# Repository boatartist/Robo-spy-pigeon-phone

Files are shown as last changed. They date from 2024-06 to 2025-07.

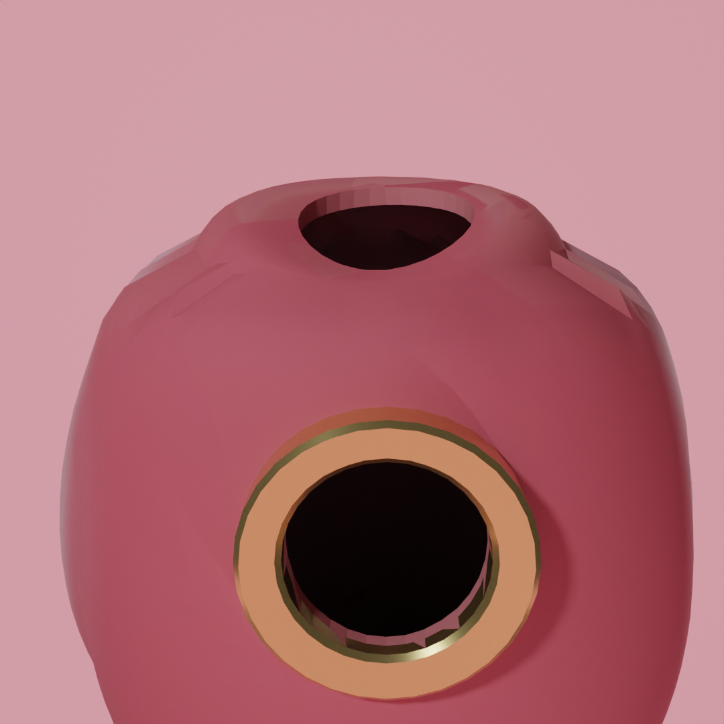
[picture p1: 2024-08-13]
Darcy_renderings/birbodyholetop1.png

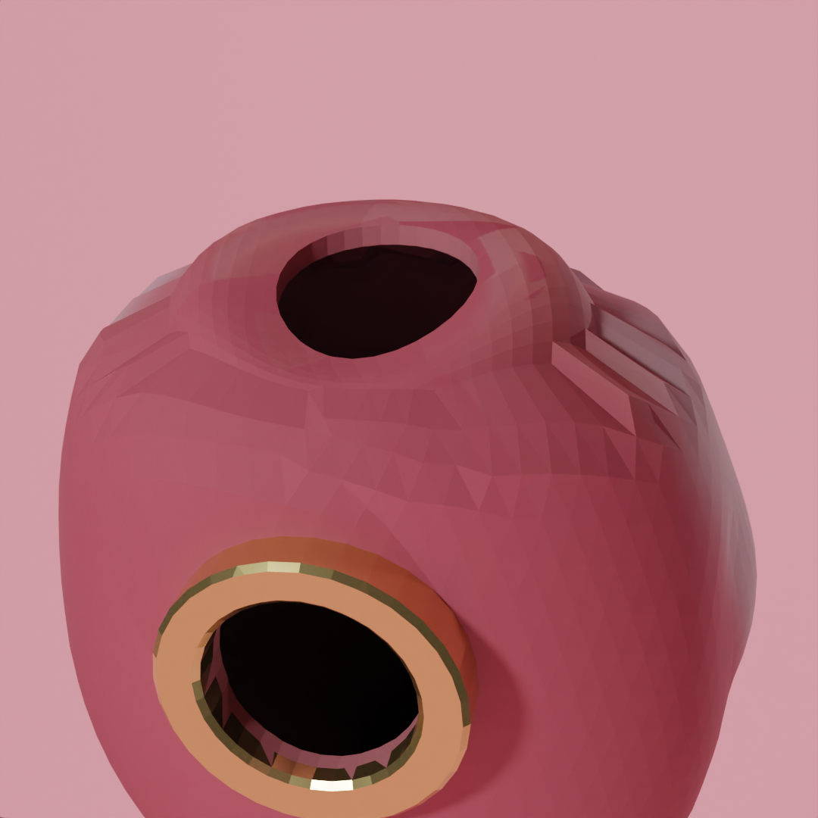
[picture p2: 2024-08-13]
Darcy_renderings/birbodyholetopflat1.png

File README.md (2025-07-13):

# Robo-spy-pigeon-phone
## May 16, 2024
Hello, welcome to my Robot-spy-pigeon-phone-assistant-project! (I'm bad at names I'll fix it later)
This is an idea I've had in my head for ages, and I really want to document one of my procrastination projects properly, so I'm just going to put everything I do onto this github, then procrastinate on my procrastination by fixing it later. 

So, robot phones. I think I was unreasonably influenced by Amy McCulloch's Jinxed series, which is a pretty good YA series in its own right. Basically the premise is that everyone has an animal-looking robot that does everything their phone used to do, and also is like a pet and friend and assistant, and idk I just think that's pretty cool. I would just make that but it'd kinda feel like plagiarism or something, which brings me to my second influence: Birds aren't real. I assume everyone has heard of this pseudo conspiracy, which is just hilarious and very much something my generation would make up in response to actual conspiracy theorists. Essentially, all birds were hunted down and killed by the US government/CIA in the 50s and 60s and replaced with spy drones that are tracking us, ooh scary. Finally: ornithopters. You know drones? They're like that but cooler, because they flap their wings. I'm not an aeronautical engineer (I'm just a highschooler actually), but I do have a very hyper plane loving little brother, so there's that

With these ideas in mind I have a bunch of features I want to implement at some point but may never, best explained through a series of tiny sketches:

WIN_20240516_12_24_25_Scan
WIN_20240516_12_25_56_Scan

Look at the little cyborg pigeon!!!❤️❤️❤️❤️ I'm so proud of my non-existent drawing skills. If you can't read my handwriting (valid, I can't either), here's some of the highlights:

- cute little perch
- holds a little pencil
- camera (or is it a death laser?)
- touchscreen
- eyes follow you around
- full 360° vision, head rotates
- foot clamps/jointed toes (taking inspiration from nerdforge's prosthetic finger but it defaults to contracted so it doesn't fall off the perch)
- Bits that move (perched edition): feet lift and flap, head rotates = 3 servos, optional bonus: balance body by tilting
- also some sound effects/comments ie. eeeee, creeeeak, ring ring..., unknown phone number...

## May 28, 2024
I made a super cute lil cardboard/electrical tape model, feeling very professional
WIN_20240528_18_45_05_Pro
And if the ultra-high quality school laptop night photo didn't sell it to you, then I used an AAA battery as a stylus to sketch over it 🙃


I also found some old(er) sketches and plans from when I wanted to make a cockatoo, so might as well put those in, there's no one reading this anyway lol

<!-- ![WIN_20240528_20_20_27_Scan](https://github.com/boatartist/Robo-spy-pigeon-phone/assets/78235705/01198416-49a5-4d13-a8f2-95e78d5ec8a3)
I probably shouldn't include that last one actually, it's kinda ruining the sci-fi super villain aesthetic I keep imagining. I don't wanna be strutting around with my cool pirate parrot pigeon phone on my shoulder acting all fancy and then get jump-scared by my 16y/o late night ramblings, but whatever. -->

## June 02, 2024 (I think, this is a retrospective post)
I tried to make a bird shape in solidworks and it went disastrously wrong. Luckily my dad is a literal designer so he showed me how to do it and mine are still terrible but i got some ideas about how to do it, later. This was the dumpy model my dad whipped up in like 10 minutes, I think mine are right at the bottom of the windows rubbish bin.



## June 09, 2024
~~Feet! (No not like that stop being dirty minded).~~ (This joke has been redacted because everyone keeps judging me (valid ig)). I figured this was as good a place as any to start my project, so I've spent this weekend wasting filament and masking tape on prototypes, until I got to a design that I think will do for now. My original concept was inspired by prosthetic finger designs (Shout out to [this video from Nerdforge](https://www.youtube.com/watch?v=ZVqa7j6jG0Q) for the inspiration), which contract when a string is yanked and then have a bit of elastic which defaults them to open again. Obviously a bird clinging to a perch for dear life has quite the opposite motivations, so my design had a bit of string on the outside which gets pulled by a servo to open the claws and then a piece of elastic pulling them closed again, as can be seen in this low-res night photo.
WIN_20240609_19_17_24_Pro
This design seemed great on paper but left more than a little to be desired in real life, so I created a new design featuring the coolest thing I know nothing about: gears. After a loooong time in solidworks I finally got something that kind of works, so my current foot design looks like this:
WIN_20240609_19_19_10_Pro
WIN_20240609_19_18_48_Pro
I'll put the current cad files up if there's anyone interested (that's a little inside joke because there's noone here at all lol)

## June 16, 2024
I figured out how to get blender on my school laptop and I've finally got a terrible low-poly model which I'm going to polish up in Solidworks (stl file up now)



This is a photo of a tiny 3D print I did of it, just for fun, I think it looks pretty good.
WIN_20240616_14_55_46_Pro
I also realised that I haven't put up the fancy drawings I did, oops, here they are now.
WIN_20240616_11_46_52_Pro
Umm, what else? Oh yes, I bought a [usb modem](https://www.telstra.com.au/internet/mobile-broadband/prepaid/4gx-mf833v-usb) to use instead of the raspberry pi hat I had for my phone project, which unfortunately broke. Hoping that having an actual professional thing will make this a bit less dodgy. 
I'm also going to buy [a little round touchscreen](https://core-electronics.com.au/128inch-round-lcd-display-module-with-touch-240240-pixels.html), which I'm really excited about, hopefully we start getting some actual progress soon!

## June 18, 2024
Welcome to the total of 2 people I shared the link to this with, here's the things I did today and at the end of the weekend.
1. I chopped the blender model in half and hollowed out the head so I could put a raspberry pi camera in there, the stl can be found on this github but it's not a final product by any means.



2. I bought a cheap usb cable and a usb socket which I soldered together so that the modem doesn't have to stick straight out of the side of the raspberry pi, instead I can attach it via the dodgy cable and position it around the side. I would advise anyone thinking of copying this project to invest in an official cable ([like this one maybe](https://www.amazon.com.au/Degree-Angled-Female-Extension-Adapter/dp/B015H0KUEI?th=1)), I melted quite a lot of plastic and had to restart several times from fragile cables breaking.
WIN_20240618_19_49_22_Pro
WIN_20240618_19_50_09_Pro

## June 25, 2024
I'm away from the Raspberry Pi rn so I can't test this code, but I've been researching text-to-speech (tts) modules that I can use, because a big feature of the bird is that it's going to give audio notifications and users will be able to converse with the robot instead of just using the screen.
WIN_20240709_15_02_11_Scan
After much consideration, I've decided to use the Google tts API (gTTS), following [this Geeks for Geeks article](https://www.geeksforgeeks.org/convert-text-speech-python/) because I'm lazy and it looks easy, but also it's really well documented and I can also use the google speech-to-text API so it will look symmetrical in my brain. According to the tutorial, this is the python code I'm going to need:
```
from gtts import gTTS
import os
tts = gTTS(text='Hello World', lang='en', slow=False)
tts.save('audio_file.mp3')
os.system('start audio_file.mp3')
```

## June 27, 2024
I got the gTTS module working, and I'm using the pygame mixer to play audio through the audio jack. I found an old pair of headphones and a speaker from a singing birthday card which I brutally massacred to make this speaker setup I can plug into the audio jack. I might replace the speaker because it's still a little too quiet, but it works for now. 



In the past I've tried to find a ready-made speaker which would do this for me, but most speakers seem to be the massive round bluetooth speakers, so anyone copying this project I would advise to find a cheap headphone jack part and a small speaker component, that seems like the best option. 
I also improved the head cad file so that the camera fits better and there's also a hole in the other eye for a 5mm led, which I think is pretty cool. I'll upload the new stl alongside the old one, they're pretty similar at this stage. I think the next step is going to be getting my hands on that round display, and also looking at how I'm going to get the microphone working, stay tuned!

## June 30, 2024
Oops, turns out I did not the gTTS working, it steals its tts from the interwebs, and mine is a bit sketchy rn, so I'm settling for a worse module that's fully offline, [pyttsx3](https://pyttsx3.readthedocs.io/en/latest/engine.html) (I did try to install it's updated sibling pyttsx4 but I'm not bothered to install the module on a computer with internet and then manually install it on the raspberry pi, so we're settling for the one I managed to get). The voices are terrible, but at least it talks and I haven't had any major issues. I also don't need to use the pygame mixer to play my sounds, so that's nice. This is my current code: 
```import pyttsx3
engine = pyttsx3.init()
# reducing the speed of the voice from 200 to 100
engine.setProperty('rate', 100)
# I think the english voice is the best, but there's code in the documentation to loop through every voice and test it if you want to find a better one
engine.setProperty('voice', 'english')
#say the thing
engine.say('Hello World, I am pigeon')
#I think the say() method preloads the audio to the engine, and then this method actually runs it 
engine.runAndWait()
```
Oh and here's a photo of the new head, it's still goofy, but I kinda love it.


## July 2, 2024
A quick moment of silent for my realisation that the raspberry pi audio jack does not support the microphone, so I apparently wasted my money and time buying [a new 4-poled plug](https://www.jaycar.com.au/3-5mm-gold-plug-4-pole/p/PP0138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), soldering 4 wires to it and trying to connect the speaker and the microphone to it, ouch. At least I did realise how I could amplify the volume of the speaker using a transistor so now we have this snazzy and compact little set-up on the back of the speaker:



And since I'm overcompensating for my laziness and refusal to make wiring diagrams for my actual school software projects, here's one I whipped up in two minutes:



So it's a bit sad that I did all that for nothing, but at least I have a good result. For now, I'm using a big flat usb mic I bought for a past project that didn't work out, but it's better than nothing until I figure out how to make my own, more compact version with the tiny microphone I bought. Oh and if anyone ever copies this project, [you can get audio output from the gpio pins](https://wiki.batocera.org/audio_via_gpio_rpi_only), which I've been searching for for ages and only discovered after hacking together my solution :( Anyway we live and we learn ig. 

## July 3, 2024
❤️ [http://apachepersonal.miun.se/~muhimr/index_files/Tutorial_4g_modem_with_Raspberry_PI_B_plus.pdf](http://apachepersonal.miun.se/~muhimr/index_files/Tutorial_4g_modem_with_Raspberry_PI_B_plus.pdf)

## July 4, 2024
I was pretty rushed when I posted that article yesterday, I hadn't done much and I just wanted to share the brilliant pdf which unlocked my ability to actually use the usb modem I've bought. So basically what I learnt is that when you go to [192.168.0.1](192.168.0.1) on any device, it takes you to your modem's page, where you can see different diagnostics, change settings and even (if you have a sim-based modem like mine) send and receive text messages. Amazing! This is the best news I've had in ever, because I thought I was going to have to hack together a solution, bypass a billion safeguards and do all sorts of wizardry to even get internet working with the modem, let alone sms on it, but no, I just need to figure out how to steal data from that webpage, praise the lord, god is good, I'm converted, all that jazz⛪✝️

... Actually, maybe not, looks like the website is kind of janky and it doesn't want me to steal from it, or maybe I'm just bad at requests and Beautiful Soup, we'll see. Oh side note I finally ordered the touchscreen watch display yesterday, so it should be here in a few days, and once it arrives I'll have all the components to start building the body (I think), stay tuned!

EDIT: I must apologise to everyone I have mislead in my claims that I was using a singing card's speaker, that **was** the speaker I experimented with, the one I'm currently using comes from a build-a-bear. I found the official product names for both (the singing card speaker is more or less [COM-15350](https://www.melopero.com/en/shop/sensors/audio/thinspeaker0dot5w/) and the build-a-bear speaker is probably [13ry328qf203](https://www.amazon.com.au/Aexit-Electroacoustic-External-13ry328qf203-Loudspeaker/dp/B07BDPJTB2)), as they seem like good options until I find a real product, but I will be using the measurements for the build-a-bear speaker in my CAD modeling.

## July 7, 2024
I was fooling around with my tts function and the audio randomly stopped working, which prompted me to have a small mental breakdown and also transfer my speaker to the GPIO pins, adding 
```dtoverlay=pwm,pin=13,func=4``` to the bottom of `/boot/config.txt`. In the end the actual problem was that raspi-config sometimes likes to have little menty-B's and change pretty standard settings, so I had to go into the system settings and [change the output back to jack](https://www.raspberrypi.com/documentation/computers/configuration.html#audio-2:~:text=passphrase%22%200%200-,Audio,-Specify%20the%20audio). Well that's good to know I guess, and it looks pretty cool and saves needing external batteries, so I'm (kinda) glad it happened. 

![image](https://github.com/boatartist/Robo-spy-pigeon-phone/assets/78235705/21720103-b9aa-44c0-8042-e7db532cf4d5)

In other news I spent way too long being bad at try-except statements and kept getting confused when raising an error caused an error to show up, but in the end I made a quick function to check for internet connection, which will be useful to switch between voices (gTTS is sooooo much better than pyttsx3, but it needs interwebs), or just to prevent errors when looking for texts or other web-based things. 
```import requests
try:
  req = requests.get('https://github.com/boatartist') #shameless self-promo
except:
  print('Uh oh no interwebs')
  #do something else here
```
Lastly, I was annotating and collating notes from the demo python code for my round display which is coming tmw (probably), I might put up those notes in future.

## July 8, 2024
EEEEEEEEEEEEEEE!!!! I just got the display and it's so cute! I'm obsessed. It is very good and once you figure out the code it's pretty intuitive, I'm going to put up a guide at some point, mostly to remind myself, but for now here's how it (more or less) works, based on [the python example](https://files.waveshare.com/upload/b/bb/1.28inch_Touch_LCD_Demo.zip) from [the official wiki](https://www.waveshare.com/wiki/1.28inch_Touch_LCD#Raspberry_Pi_User_Manual) (thank you Waveshare ily <3):

(nvm I moved it to a file of its own because I kept coming up with improvements, check out the code example in `code/round_display_demo.py`)

## July 9, 2024
I *think* that I've finally gotten to the bottom of the stupid audio error, which was based on the raspberry pi not defaulting to the right output, after completely overhauling my entire tts setup haha. In trying to fix my setup, I've moved to a different tts module (again), which is espeak. Actually I didn't really change anything, I'm just using the command line interface rather than the pretty library setup to run it for me. What I did was identify the sound card and device number of my speaker by running `aplay -l` in the command line, and then to output text I give the command line this: `espeak "Some text" -s 120 -ven+f3 --stdout | aplay -D hw:2,0`, which is a lot of fancy symbols for, "espeak please say 'some text' at 120 wpm with the third english female voice" followed by "aplay please play this out of sound card 2 device 0". Oh yeah I found more voices which is nice, I can even make it ✨whisper✨ ooooooh. So that's fun. 

In other news my round display is working great, I made a class for it so I didn't have separate touch, display, image and draw objects, I'll post that in the code folder. At the moment I'm working on making a menu that shouts at you but doesn't keep shouting (I don't know why it won't shut up 🫠), but at least we're going somewhere. I also found that there are lots of pretty colours, because PIL uses the html colour list, which is very expansive and a great opportunity for me to demonstrate my lack of graphic design skills, yay!
Here are some photos from my experimentation:





## July 11, 2024
Yesterday my brain said: "Do some CAD modeling", so I did that even though I didn't have a mouse or any plans, leading to the jankiest prototype ever, but I've got a mouse-adaptor now so I'm going to fix it, but for now I'll put up all the files in a folder:





## July 22, 2024
It might be easy to think, from the fact that I haven't updated this page in 11 days, that I've been busy doing schoolwork and not procrastinating, but no that would be a mis-guided naive optimism. In fact, I told myself that I would not work on this project until I'd finished my homework, which was a sure-fire way to ensure I worked on it constantly during momentary lapses in my willpower. So, what have I achieved? 
1. I made a blocky little case to think about positioning and hold the screen up while I messed around with some code, not sure if it was worth it but it looks cute (or it did before I melted holes in it for all the ports I forgot I needed access to).
   


2. The audio stopped working (again) and I realised that, although using the GPIO pins is very convenient, it only produces square wave digital outputs, which is a bit too janky, so I reverted to using the 3.5mm jack, which is a bit annoying but it does link to my next point
3. I thought a **lot** about how the user could change between audio output modes, experimenting (unsuccessfully) with having a bluetooth mode, which I might come back to later, but in the end I came up with a decent solution, which basically has a socket into which you can plug in wired headphones at any time, they don't turn off, and also a switch/settings option to turn off the built-in speaker by way of a GPIO pin which provides power through my fun transistor solution from earlier.
4. So obviously that meant that I bought a 3.5 mm socket, a usb socket, a couple of switches, and a prototyping solderable board. That last part is the most useful, as it lets me combine all the components, and it was also incredibly convenient because I put all the pins from the display in a line, so I no longer have to worry about the fiddly order every time.


I think I messed up the speaker somehow, might be the transistor, but it's looking better already.
WIN_20240722_13_20_55_Pro
WIN_20240722_13_20_48_Pro

Once I've fixed the built-in speaker I'm going to install the sockets and switches, which will be able to be moved to wherever I want my peripherals, I'm thinking under the wing in the final product, that would be cute. Another plan I have for the end is to get a custom PCB made, which will plug all my components in really nicely and easily, and look a bit smaller and more professional, but I should probably get my prototype working first. I feel like there was some code I did, but I don't think I have any big updates.

Oh, that's right, I wanted to shout out the guys at Core Electronics, the online store where I've been buying a lot of my stuff, because I sent them a really wacky and unedited email asking them whether this project might be worth getting published on their projects section one day, and they came back in a couple of days with a really helpful and encouraging email about how I could transform this blog/log thingo into a proper tutorial, which I'm really grateful for and will definitely be applying when I get around to finalising all the documentation. Thank you! :) 

## August 4/5, 2024
The speaker not working was apparently just because I used the wrong transistor by accident, oops. I think it would have worked if I'd turned it around, but for consistency's sake we're sticking with the BC557, which is a PNP rather than the NPN BC547 I accidentally used. So that's good news, we now have the speaker shouting at us, and it turns off when it's not, so that there's no buzzing.
WIN_20240804_15_00_18_Pro
This means that I almost have enough functionality to mock up another prototype, but I might quickly solder my sockets first, and put in some header pins for servos. I am a little worried because I only have about 3 GPIO pins, since the prototyping board only includes the first half of the pins, but I think this should be enough to do claw movement and maybe head rotation, which is quite exciting. 

Things I need to fix/do (as of my brain rn):
- solder all sockets (3.5mm audio and usb input, maybe hdmi at a later date)
- stop the screen from freaking out and thinking that I'm infinitely pressing wherever I last pressed, I just want to press once and then it stops
- get a useable requests interaction with the modem's webpage, so that I can send and receive texts without using minicom, since the fancy modem is based on windows software. (alternatively I could invest in a less sophisticated/linux compatible modem that does use minicom)
- look at making a pcb/getting a new and bigger prototyping board
- figure out camera -> display live streaming, this should be possible but it doesn't seem to like it
- consider balance, weight and how complex the design should be, so that I stop wasting filament and am more consistent with my design
- possibly remarket the pigeon as a galah, because they're much prettier, their heads are bigger and closer to their bodies, and if I sell them in Australia one day I can frame it as a limited edition native birds line
- start documenting this project properly before it gets too chaotic (I probably won't do this tbh)

## August 11, 2024
I figured out how to stop the display taking infinite input, by reasoning that it probably wasn't a problem unique to my project, and that it likely just doesn't reset to 0,0 ever, despite my best hopes. Basically, when you press the display once, it reads that and keeps outputting it forever, or until there's a new input. To counter that I kept track of the previous input and have a flag which says if there's been any new input to worry about.

With this problem under control, I optimised (slightly) my code and put it in a class, I'll replace previous code uploads with the working current files, you can turn the speaker on or off, change the wifi mode, and listen to the speaker scream at you if you press any function which isn't active yet, I'm pretty impressed with myself. `bird.py` is the main file, and it imports all the other modules including `offline_tts`, `display`, `wifi` and `check_for_internet`. Remember that display also imports the display's module, so if anyone is running this and getting errors, it's probably that. At some later date I'll look into how requirements.txt files work, because there are a lot of random modules to import, and if anyone is ever copying this project I don't want them to have to debug everything line by line. 

I also implemented the camera app, apparently the only thing I needed to change was refreshing the stream every time, but it now works, showing an only slightly laggy feed from the camera, which saves to `final.jpg` on the Desktop (or wherever the main file is) when you click the screen, I'm pretty happy with it. :)

I still don't have a plan for the modem, I think I might have to put my issue on stack overflow, but that's definitely a last resort. In the meantime, I'll keep weighing up the value of just getting a software-less modem, stay tuned!

## August 13, 2024
I am incredibly excited rn, because I showed this project to my awesome friend Darcy a little while back, and she's offered, with all her amazing DT, CAD and Blender skills, to design all the cases for my newly rebranded galah, because she actually knows how to make it look incredible. I'm going to have to give her all the specs, but she's already mocked up a ✨stunning✨ aesthetic prototype, look at it!!! I'll put all the screenshots/renders she sent me in a folder, but here are some of the highlights :)
Birb1angle
Birb1front
birbflat1
birbodyholetopflat1
birhed1

EDIT:

Stack Overflow is the best thing ever and I may have solved all of my modem problems. Literally, I posted [a question](https://stackoverflow.com/questions/78864009/is-there-a-way-to-access-the-sms-capabilities-and-modem-webpage-of-a-usb-4g-mode) and mere minutes later a response from a bored computer scientist popped up, suggesting that I use Selenium to dynamically load the webpage, which I think might be exactly what I needed, so good!

## August 14, 2024
Heh heh heh, it's 9pm on a school night and I only just managed to install all the correct drivers for selenium, but (I think) it's finally ready to actually use, yay! I spent just a little itsy bit of time crying dejectedly when the raspberry pi was being a stupid little child and not being okay with any of the normal procedures, but after searching up something along the lines of 'How to Selenium Raspberry Pi Python beginners easy guide diy step by step someone else do it for me' I *finally* found [a useful tutorial](https://patrikmojzis.medium.com/how-to-run-selenium-using-python-on-raspberry-pi-d3fe058f011). No well actually it was [the link in the comment on that tutorial](https://ivanderevianko.com/2020/01/selenium-chromedriver-for-raspberrypi) which solved my problem but whatever. If anyone wants to know how to install selenium and all it's required drivers, here's what I've learnt (against my will), as a quick 2-step method.

Step 1: Install the actual Selenium module: `pip3 install Selenium`

Step 1.1: Doubt yourself when this doesn't immediately work and install all sorts of different versions, only to realise that this was not at all the problem

Step 2: Try to install all manner of legitimate Firefox and Chrome drivers

Step 2.1: Get desperate and try illegitimate and vaguely sketchy installation methods for said drivers, looking for the right version which matches the version of your browser (you can find what this should be with `chromium-browser --version`)

Step 2.2: Find a more genuine way and finally get the right driver which magically has the correct version and you didn't need to scroll through 50 pages of releases `sudo apt-get install chromium-chromedriver`

Step 3 (extra fun bonus): Use `chromedriver --version` to check that you've got it right all in one and try to push back exhausted tears as you rush to document this because otherwise it's bound to get lost and have to be re-done. Yippee! 🙃✨❤️ 

While I was being optimistic and hadn't tested for base functionality I started coding a function to log into and retrieve data from the website, so I might be able to finish it tmw and implement it slightly, but it's 9.25, I should probs go to bed now.

## August 15, 2024
So, even though Selenium and I are besties now, the telstra webdesign people are my opps, with their user-friendly complex html layouts, unbelievable, smh. I would like to introduce these people to high school students and the level of complexity that there is not in any of my html endeavours, but I guess I'll just have to deal with it. It is going relatively well tho, and for paranoia about losing files sake I'm gonna paste the dodgy thing I've got here: 
```
#password input: id=txtPwd, password = Admin
#login button: id=btnLogin
#each text conversation on the main page's id starts with smslist-item- then a long number
from selenium import webdriver
from selenium.webdriver.common.keys import Keys
from selenium.webdriver.common.by import By
import time

print('installed the things')
#driver = webdriver.Chrome(ChromeDriverManager().install())
#driver = webdriver.Chrome('/usr/bin/chromedriver')
driver = webdriver.Chrome()
print('driver exists')
driver.get('http://192.168.0.1/index.html')
print('got a webpage')
try:
    login = driver.find_element(By.ID, 'txtPwd')
    login.clear()
    login.send_keys('Admin')
    login_button = driver.find_element(By.ID, 'btnLogin')
    login_button.click()
except:
    pass
while True:
    try:
        sms_link = driver.find_element(By.LINK_TEXT, 'SMS')
        sms_link.click()
        break
    except:
        pass
try:
    right_sms_mode = driver.find_element(By.LINK_TEXT, 'Device SMS')
    right_sms_mode.click()
except:
    pass
while True:
    try:
        new_sms_button = driver.find_element(By.ID, 'smslist-new-sms')
        new_sms_button.click()
        break
    except:
        pass
while True:
    try:
        contact_input = driver.find_element(By.ID, 'chosenUserSelect_chzn')
        contact_input.click()
        break
    except:
        pass
contact_select = driver.find_element(By.CLASS_NAME, 'chzn-results')
contacts = {}
try:
    for i in range(59):
        person = driver.find_element(By.ID, f'chosenUserSelect_chzn_o_{i}')
        name = person.get_attribute('value')
        contacts[name] = f'chosenUserSelect_chzn_o_{i}'
except:
    pass
for name in contacts:
    print(name)
contact = input('Contact: ')
contact_input = driver.find_element(By.ID, 'chosen-search-field-input')
contact_input.send_keys(contact + Keys.RETURN)
message = input('Message: ')
text_input = driver.find_element(By.ID, 'chat-input')
text_input.send_keys(message)
send_message = driver.find_element(By.ID, 'btn-send')
send_message.click()
time.sleep(60)
driver.close()
```

So ja, it's a bit special and sometimes it lags a whole bunch so I have to implement dodgy loops, but this code *mostly* works, except for some reason the contacts don't like me and that's still broken, but I can navigate to the texts page and try to send a message, just to nobody. So yay! 

Oh and I also remembered, I'm gonna take my setup to school tmw and Darcy might have a look at measuring and designing stuff (maybe). 

## August 23, 2024
I bought [a super cheap usb microphone from officeworks](https://www.officeworks.com.au/shop/officeworks/p/otto-usb-c-wired-lapel-microphone-otcck15lm) to look at getting speech-to-text, and I can now record audio and interpret it using the speech-recognition module and google speech recognition. However, I didn't have much luck with the module's built-in microphone, and I don't want to have to rely on an internet connection to be able to talk to the robot. So then I messed around with mozilla deepspeech and sopare, and neither of those were very good either. I was just about to give up when I found [vosk](https://alphacephei.com/vosk/), which is a miracle and now I have speech to text:
```
import os
import time
def get_audio(length=5):
  os.system('arecord --device=hw:2,0 --format S16_LE --rate 48000 --duration={length} test.wav')
  print('got audio')

def translate():
  try:
    os.system('vosk-transcriber -i test.wav -o test.txt')
    f = open('test.txt', 'r').read().strip('/n')
    return f
  except:
    print('error')
    return None

while True:
  input()
  get_audio()
  time.sleep(2)
  translate()
```
This isn't implemented yet because I'm not really sure what the best way to record the audio is, whether I can tie it to a button being held down or record for a set time after recording, or whether it's best to listen all the time. Not hugely keen on the last two, but we'll have to see what I dig up. My solution is also quite file-heavy, but I think it should be possible to bypass the audio file like with the tts, we'll see.

## August 24, 2024
I finally got around to changing the settings page to include an internet status and abandoned the idea that you might plug in headphones to a literal bird. I also made a very janky little interface for the notes app where you can speak for 5 seconds and get some text saved to a file, just as a proof of concept really, it's not very useful rn. But I'm feeling very happy that I unlocked another feature, even if it isn't perfect. The stt functions and updated code have been uploaded, and I also uploaded a requirements.txt file. I found a geeks for geeks article which had an automated function to create one, so this is just what it spat out from the folder of all of my code, but this doesn't include command line modules that I access through the os module, and assumes that you run all the code as it exists in the code folder on this github, including having the display functions in the lib folder, so I'll see how I can improve it to make it more useful later on. Anyway, here's some photos of the most recent interfaces (I think I wasn't close enough to the mic, it doesn't seem to have picked up my 'hello this is some test audio' very well but at least it got something) :





## September 04, 2024
I've spent a *lot* of time recently researching power methods, because it occured to me that this is going to need to be wireless, and the shape of the thomas the tank engine battery pack we found in the park isn't going to cut it. 



So I need to make my own battery charger circuit. There are heaps of boards online, and my only requirements are that they supply at least 5V and 2.5A, and have sockets for charging and powering the pi. [This one from Core Electronics](https://core-electronics.com.au/mp2636-power-booster-charger-module.html) looks pretty good, but I'm not 100% sure if that's the best option. If I get that board or similar, I can use a few rechargeable Li-ion batteries from my local Jaycar, but I can also get some online if there's a different shape I need. 

Another option, which seems just an itsy bit dodgy is to use this board I stole from an old drone:



It's super tiny, which is great, but I have no idea if it will work or just catch on fire. At any rate I'd have to botch together a supicious cable for powering the Pi. Also, I just read the specs from the battery casing (I had to bin the original battery because it was on the brink of explosion), and it says that it outputted 3.7V and 600mAh. Sooooo, that's probably not enough, but a fun idea nonetheless. I will continue looking for stingy ways to make this powerbank, and I also realised that I have no sort of tilt sensors, so I'll look for some of those at the same time. Finally, I want some smaller servos, so I'm going to hunt down a hobby/rc store and find some. 

## September 07, 2024
I went to Jaycar to look for some batteries and I ended up getting [a battery charger](https://www.jaycar.com.au/duinotech-arduino-compatible-lithium-battery-usb-charger-module/p/XC4502), [a 5V output board](https://www.jaycar.com.au/duinotech-arduino-compatible-5v-dc-to-dc-converter-module/p/XC4512) as well as [a 3.7V 2600mAh Li-Ion battery](https://www.jaycar.com.au/18650-rechargeable-li-ion-battery-2600mah-3-7v-solder-tag/p/SB2313). So that's a great haul which I combined into this dodgy little circuit which hasn't fully caught on fire yet, it only smoked once when I touched both ends of the battery together through my third hand.



While it is outputting the required 5V, it doesn't seem to have very much current, I managed to charge my phone by 2% over half an hour, but it didn't fully turn on the Raspberry Pi and I turned it off as it got pretty hot while charging, by attaching a random switch I had. I'll try attaching more batteries in parallel, but in the meantime I'm just keeping it away from flammable materials and searching for alternatives. 

In other news, I found some coreflute my brother was hiding and I used it to make a super basic model of the galah shape so that I can do some feet later. I had lots of fun layering bits of scrap to make a round head, and I reckon it looks pretty good!









## September 20, 2024
Took a huge risk yesterday and edited the `/home/pi/etc/rc.local` file so that the program runs on startup, which is very stressful and last time I tried to do that my raspberry pi died and I had to create a new micro-sd card with an image and buy an sd-card adapter to remove the edit so it would turn on again. This was very traumatic, I would not recommend. But this time I spent ages debugging and ended up adding `sudo python3 /home/pi/Desktop/galah/bird.py &` to the file, and also added some absolute path references, but now it does that. 
I also tried to improve my claw design by making it smaller so it grips smaller things, but this did not actually do anything, I think I need to add joints to the foot and make it less gear-slippy. But it looks pretty cute sitting dangerously on top of my monitor.




## November 19, 2024
Oops it's been a while since I posted. Haven't done much, I think. Actually no I did some code a while ago but I didn't get around to documenting it. I used a weather API and the datetime module to make a timed out screen. 


All the code for that is in the files, maybe I changed something else I don't remember.

More recently, I bought some armature wire and made a new wireframe of the shell, to think about scaling and stuff in a more 3D way after my coreflute adventures were a bit of a flop. I'll probably paper mache over it or something, but it's quite pretty sitting on my desk for now.
WIN_20241116_18_14_46_Pro
WIN_20241119_19_11_23_Pro

Note for self: researched into raspberry pi's rules about using it in product, I only need to put "Powered by Raspberry Pi" or similar on the packaging [link](https://www.raspberrypi.com/trademark-rules/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), [other link, make sure to actually apply](https://www.raspberrypi.com/for-industry/powered-by/)

## December 10, 2024
I've been doing lots of planning on the products.md file, so there are tutorials and links over there, as i'm about to order my next batch of stuff and also am going to make a pcb (i'll document it soon). [This lifesaver tutorial didn't quite fit over there but most of my planning does](https://www.instructables.com/Raspberry-PI-Multiple-I2c-Devices/). 

Here's a preview of my pcb! There're probably some huge flaws, but i'm very excited already!



## December 12, 2024
Past me is such a clever little cookie :) Very glad I checked my code and wiring for the speaker. Combining the resistor-capacitor circuit I found this week with the transistor circuit I had before, we now have an effective GPIO-based audio output speaker that I've (almost) integrated into the PCB. Just to remind myself, we're using GPIO 13 for the signal (`dtoverlay=pwm,pin=13,func=4` in `/boot/config.txt`), GPIO 24 for extra power and also turning the speaker off, and the wiring diagram I put in `products.md`, which I might as well copy over. Anyway, I've asked for most of the components for (and including) the new Pi for Christmas, and I'll order the PCB asap, very happy ❤️❤️.

WIN_20241212_16_03_36_Pro

(NB: I need to check that all code is updated, there's probably a super efficient way for me to copy it all over from github, I don't want to take up too much processing power/memory on the Zero with finnicky things like logins).

!! Oops sorry scratch that, GPIO 24 is being used by the accelerometer, using GPIO 12 instead

## December 31, 2024 / January 1, 2025
Happy New Year everybody! This seems like the perfect time to do a stock take and collect myself, as I've done a lot of different things this year that I need to organise and document properly. Also, I got all my components from my wishlist for Christmas.

WIN_20250101_09_13_06_Pro

So, what's going to be in the galah?
- Raspberry Pi Zero 2 W
- Waveshare Round 1.28inch Touch LCD
- 3.7V 2000mAh LiPo battery
- Telstra LTE 4GX usb modem
- Raspberry Pi camera
- Raspberry Pi camera cable for Pi Zero
- SD card with Raspbian OS for Pi Zero
- USB microphone
- Adafruit Mini USB 4-Port Hub
- Adafruit PowerBoost 500 Charger board
- ADXL345 Accelerometer
- 3 x 9g micro servos
- Mini HDMI to HDMI adapter
- solderable USB sockets
- custom PCB HAT (TBC)
- small speaker/piezo buzzer
- BC557 transistor (for audio amplification)
- 10uF electrolytic capacitor
- 150 ohm resistor
- 270 ohm resistor
- 33 nF ceramic capacitor
- male and female header pins (lots idk how many)

Also possibly needed:
- hdmi cable
- usb mouse and keyboard
- monitor
- micro-usb power source for charging
- soldering equipment
- optional led or sensor for eye

Next up, software settings:
- Raspbian OS for Pi Zero 2 W
- connect to home wifi
- connect to modem by going to `192.168.0.1`
- raspberry pi configuration enable SPI, I2C, set timezone and locale
- alsamixer confirm microphone connection
- open config.txt with `sudo nano /boot/firmware/config.txt` and add `dtoverlay=audremap,pin=13,func=4` to the bottom, as well as `dtoverlay=i2c-gpio,bus=4,i2c_gpio_delay_us=1,i2c_gpio_sda=23,i2c_gpio_scl=24` where spi is enabled, then save and close
- install all python modules with `sudo apt install python3-xyz`, where xyz is the name of each package, (pip is broken in newer versions of raspbian so we need to do it one at a time)
- install espeak with `sudo apt install -y espeak`
- install vosk (stt) with `pip3 install vosk --break-system-packages` (yes it's a bit sketchy but it didnt' work with python3)
- install picamera `sudo apt-get install python3-picamera2 python3-picamera2` (change this in the code, picamera is outdated we need the new version)
- download all the code and put it on the desktop; command line: `wget https://github.com/boatartist/Robo-spy-pigeon-phone/raw/refs/heads/main/galah.zip`
- check all path names are right by running code on the command line `python3 /home/pi/Desktop/galah/bird.py` (or whatever the file is called)
- run the code and make any changes you need to, there may be compatibility errors
- (change the gpio pin for the speaker power from gpio 24 to gpio 12)
- right click on the audio icon in the top right of the screen, increase the volume, in device profiles turn off hdmi audio and check that av jack is enabled in stereo.
- edit `/home/pi/etc/rc.local` and add the line `sudo python3 /home/pi/Desktop/galah/bird.py &`, which should make your code run on startup but in the background so that if it crashes you can still use the raspberry pi

I think that's it, but I'll have to confirm once I have the PCB and run it through for real. Fingers crossed 🤞❤️✨🦜

looking at how to connect to any wifi network over the command line: [connecting to a network](https://fleetstack.io/blog/raspberry-pi-connect-to-wifi-command-line), [finding available networks](https://retropie.org.uk/docs/Wifi/#:~:text=To%20scan%20for%20WiFi%20networks,along%20with%20other%20useful%20information)

## January 7, 2025
hehe guess who ordered the wrong version and now finally has 5 of the wrong pcb ❤️. Actually it's not *that* bad, but this prototype doesn't have the transistor or the accelerometer in the right way, might order a new one. It does looks pretty cool tho.



## January 8, 2025
Was trying to install accelerometer code but it needed a whole bunch of non-existent libraries (very annoying that pip doesn't work anymore), so I found [another tutorial](https://how2electronics.com/measuring-acceleration-with-adxl345-accelerometer-raspberry-pi/) and put the code on this github, will test later. 

I was also thinking about how I can improve my PCB before I reorder it, I've got the LCD working after some dodgy soldering had me doubting my entire program, but I still think I'm going to make all the paths wider and I actually like the positioning of the accelerometer over the board, very cute and more compact.

Another discovery I made was that we can put a switch on the output of the power boost module to turn off the output but still allow charging, which we definitely need all the time because the discharge is faster than the charge or something. When we do that I just need to put a switch between the EN (enable) pin and ground, which is a much better option than what I was thinking of doing (ie. cutting the battery cable and putting a switch in there), and it won't have to bear all the current from the battery.

‼️Reminder to myself to charge the battery fully whenever I can, I've never seen it at full charge but there should be a green LED when it is.

‼️Another reminder that I need to look at the resistor-capacitor circuit on the speaker, there might be a more advanced and better version because rn it is very bad.

## January 9, 2025
Am making a tensorflow/teachable machine based letter identifier to mimic the apple watch draw to type functionality, but have been having issues trying to install tensorflow lite to actually use this module, [this tutorial](https://pimylifeup.com/raspberry-pi-tensorflow-lite/) seems like my best hope so far but idk it's not quite working.
Yk what, we're just going to break the rules, install tensorflow lite with `pip3 install tflite-runtime --break-system-packages` 

## January 20, 2025
Things I have done that I forgot to document (all code is updated tho)
- created the file `/lib/systemd/system/bird.service` which auto-runs the program on startup, I'll put that in the code somewhere.
- fixed the camera app to run without a monitor using a different Preview
- created a camera menu, featuring options to photograph, video (unimplemented) or view images in a gallery
- finished making the draw-to-type notes app, only with lowercase and spaces so far
- used ssh instead of switching monitors between my pi and desktop ;)

## July 10, 2025
(Note to self, to use ssh with desktop type `ssh pi@192.168.0.81` with password galah.) Oh damn it's been a while, HSC huh.

I want to get the accelerometer balancing servo thing working, so I've done a lot of tinkering with that, including getting the pitch and roll shown on the home screen and when that wasn't the issue I did some research into the servo so in the next pcb it will be powered from the 5V not the 3.3V pin, and I'm going to try changing the maximum and minimum pulse widths to the defaults according to [this useful webpage](https://picockpit.com/raspberry-pi/servo-pico-w-pulse-width-modulation/) which has a datasheet for the SG90 microservo that I'm using. [This](https://gpiozero.readthedocs.io/en/stable/api_output.html#angularservo) is the link to the AngularServo API.

Completely forgot the name of the PCB software, which is Easy EDA, so I'm trying to type out all the important things to be able to search so that doesn't happen again. 



Wiring diagram if you're into that sort of thing, needs improvement ik.

I'm using a paperclip to bridge between the EN and GND pins on the DC converter/battery charger board to stop it losing charge instead of the permanent switch or disconnecting the battery from the board.

## July 13, 2025
Yes, I am very fancy. For proof, see how well I've updated the wiring diagram it is absolutely stunning.

Schematic_galah-pcb-for-pi-zero_2025-07-13 (1)

This manifests in a very nice looking PCB as well (Gerber in files).



And of course, I've finally given up on making claws and we have a very nice balancing platform for the components which *hem hem* auto adjusts to keep everything level. The platform is secured to the base at the servo and another pivot at the back, so it's nice and stable, and I've used actual screws to mount the servo, and some M2.5 bolts I had lying around to mount the screen. (actually that last part is slightly untrue because it's mounted by the one screw I could find and a spacer, but I'll get there). 





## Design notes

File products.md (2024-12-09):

# All of the components I have used/wish to use:
## Currently in use:

[Raspberry Pi 3B+](https://core-electronics.com.au/raspberry-pi-3-model-b-plus.html)

[Raspberry Pi camera](https://core-electronics.com.au/raspberry-pi-camera-board-v2-8-megapixels-38552.html)

[Round Touchscreen LCD Display](https://core-electronics.com.au/128inch-round-lcd-display-module-with-touch-240240-pixels.html)

[Raspberry Pi prototyping HAT](https://www.jaycar.com.au/prototyping-hat-for-raspberry-pi/p/XC9040)

[ZTE/Telstra USB 4G modem](https://www.officeworks.com.au/shop/officeworks/p/telstra-prepaid-4gx-usb-modem-telmf833v)

[USB microphone](https://www.officeworks.com.au/shop/officeworks/p/otto-usb-c-wired-lapel-microphone-otcck15lm)

[Build-a-bear speaker (not the exact model)](https://www.amazon.com.au/Aexit-Electroacoustic-External-13ry328qf203-Loudspeaker/dp/B07BDPJTB2)

[Micro servos](https://www.jaycar.com.au/arduino-compatible-9g-micro-servo-motor/p/YM2758)

Sketchy audio cable featuring [this plug](https://www.jaycar.com.au/3-5mm-gold-plug-4-pole/p/PP0138)

Lots of header pins

Generic LED for other eye

### Prototype power system:

[3.7V Rechargeable Li-Ion Battery](https://www.jaycar.com.au/18650-rechargeable-li-ion-battery-2600mah-3-7v-solder-tag/p/SB2313)

[SPST Switch](https://www.jaycar.com.au/spst-mini-rocker-switch/p/SK0984)

[Battery Charger Board](https://www.jaycar.com.au/duinotech-arduino-compatible-lithium-battery-usb-charger-module/p/XC4502)

[5V Output board](https://www.jaycar.com.au/duinotech-arduino-compatible-5v-dc-to-dc-converter-module/p/XC4512)

## Possible future purchases

[Raspberry Pi Zero 2 W](https://core-electronics.com.au/raspberry-pi-zero-2-w-wireless.html)

[USB Hub](https://core-electronics.com.au/adafruit-ch334f-mini-4-port-usb-hub-breakout.html)

[Accelerometer to measure tilt angle](https://core-electronics.com.au/adxl345-triple-axis-accelerometer-gy-291.html)
[tutorial for accelerometer maybe](https://pimylifeup.com/raspberry-pi-accelerometer-adxl345/)

Joystick/buttons for alternative to touch-screen control

Custom PCB for all components

Other connectors for usb, power, and hdmi peripherals

[When I buy the Pi Zero I will need to get GPIO audio output, and this tutorial will help me make it sound better than it does rn](https://learn.adafruit.com/introducing-the-raspberry-pi-zero/audio-outputs), [or i could use this one](https://shallowsky.com/blog/hardware/pi-zero-audio.html)



## 29/11/2024 - researching better power options
[nice charger](https://core-electronics.com.au/makerverse-usb-c-lipo-charger.html)

[good battery maybe](https://core-electronics.com.au/polymer-lithium-ion-battery-2000mah-38459.html)

[handy website](https://www.circuitbasics.com/how-to-power-your-raspberry-pi-with-a-lithium-battery/)

i can probs use the dc-dc converter i already have

[awesome adafruit module but why is it 40 bucks i want this but not this price, that's more than the pi zero](https://core-electronics.com.au/powerboost-1000-charger-rechargeable-5v-lipo-usb-boost-at-1a-1000c.html)

[ooh this is the same but cheaper](https://core-electronics.com.au/powerboost-500-charger-rechargeable-5v-lipo-usb-boost-at-500ma.html)

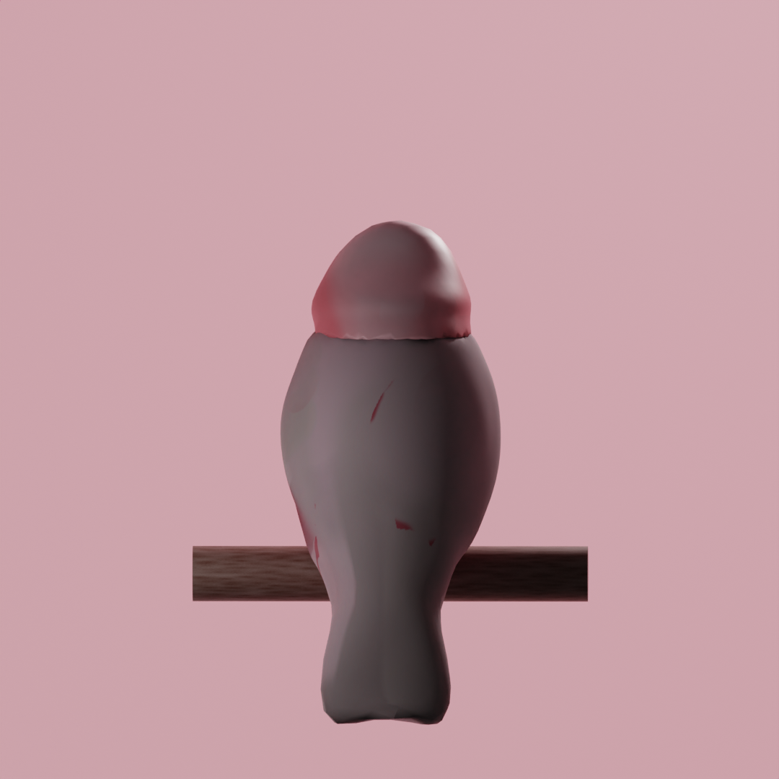
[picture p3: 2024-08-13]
Darcy_renderings/Birb1back.png

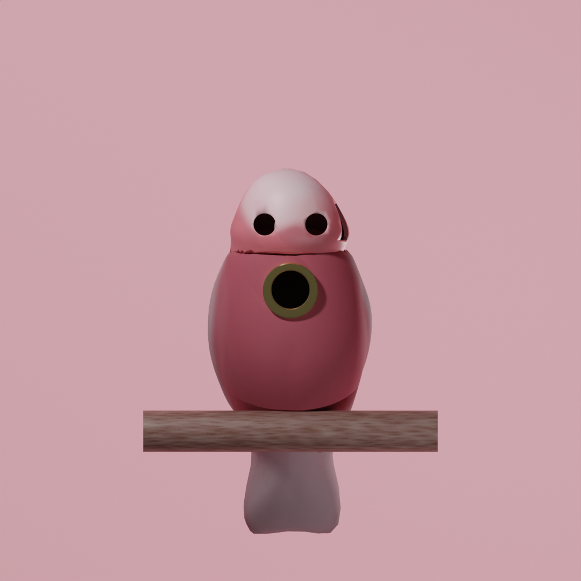
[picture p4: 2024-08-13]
Darcy_renderings/Birb1front.png

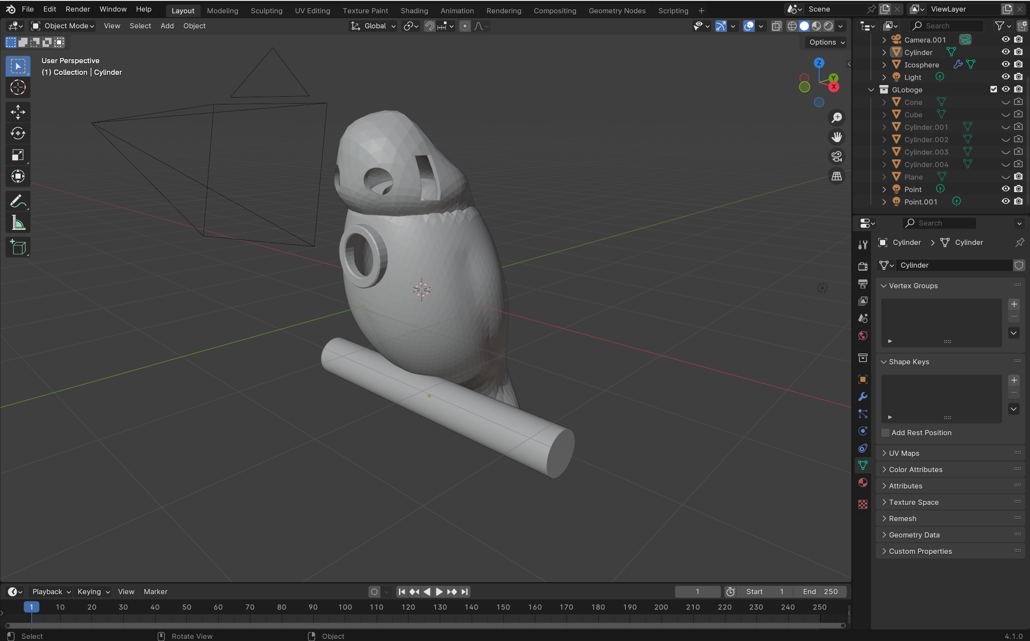
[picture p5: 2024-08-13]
Darcy_renderings/Blender screenshot for arabella.png

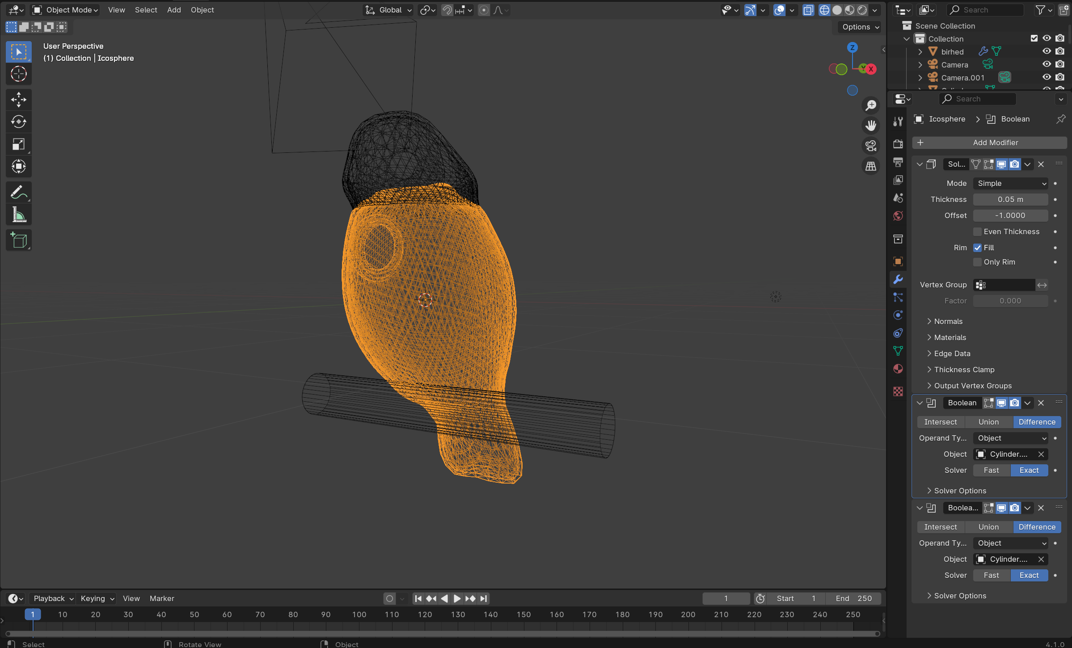
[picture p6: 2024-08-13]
Darcy_renderings/Blender screenshot for arabella 2.png

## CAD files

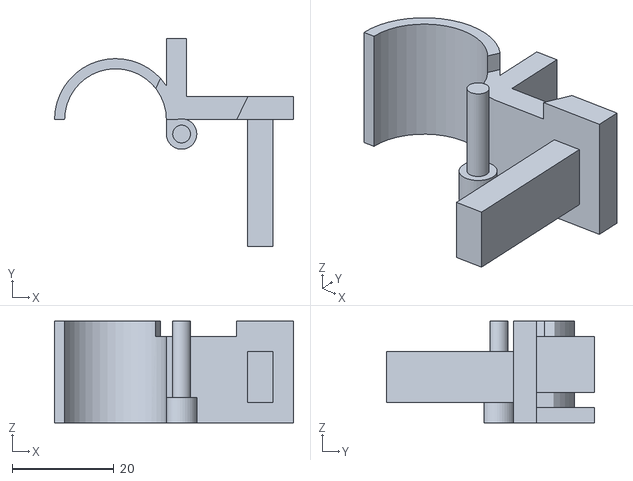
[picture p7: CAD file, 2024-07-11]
CAD files/july11_all_files/gripper v2 main part.STL
47.0 x 41.0 x 20.0

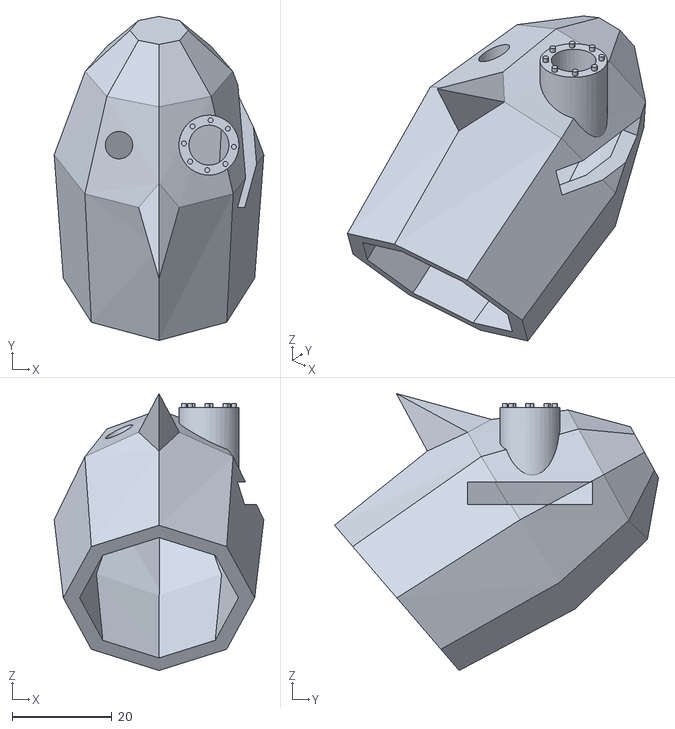
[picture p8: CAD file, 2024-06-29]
CAD files/birb_head2.STL
42.0 x 64.8 x 55.5

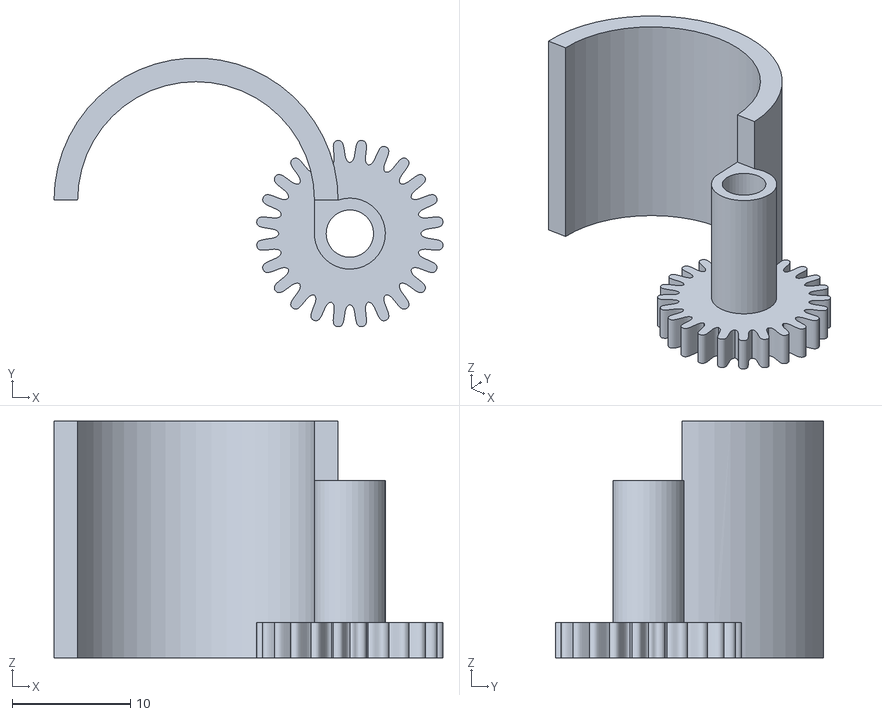
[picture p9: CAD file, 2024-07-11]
CAD files/july11_all_files/gripper v2.STL
32.9 x 22.7 x 20.0

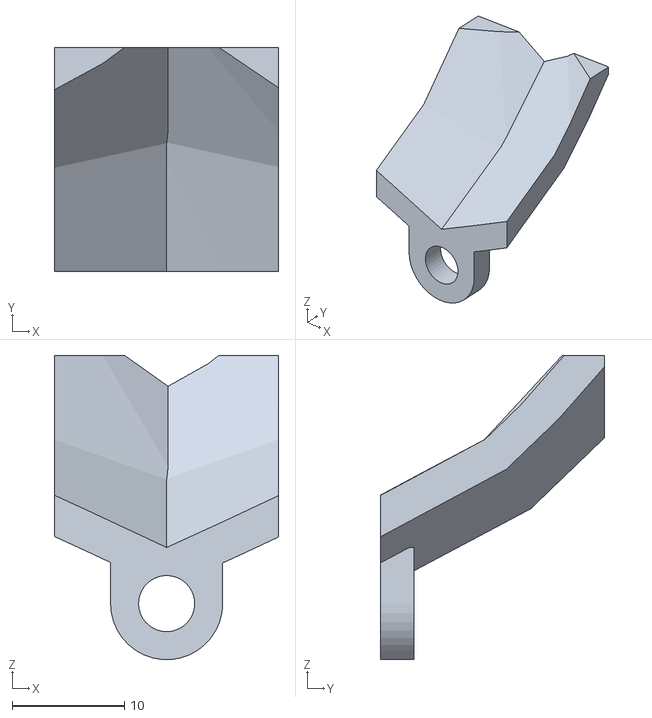
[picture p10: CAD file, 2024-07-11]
CAD files/july11_all_files/birb_head_flap.STL
20.0 x 20.0 x 27.1

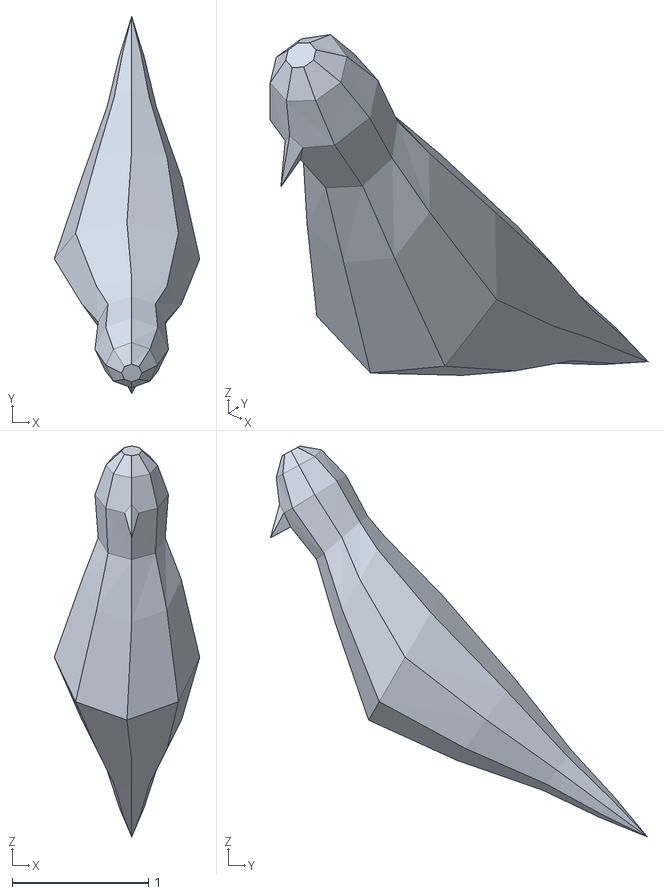
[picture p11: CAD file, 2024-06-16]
CAD files/bird_basic.stl
1.07 x 2.77 x 2.87

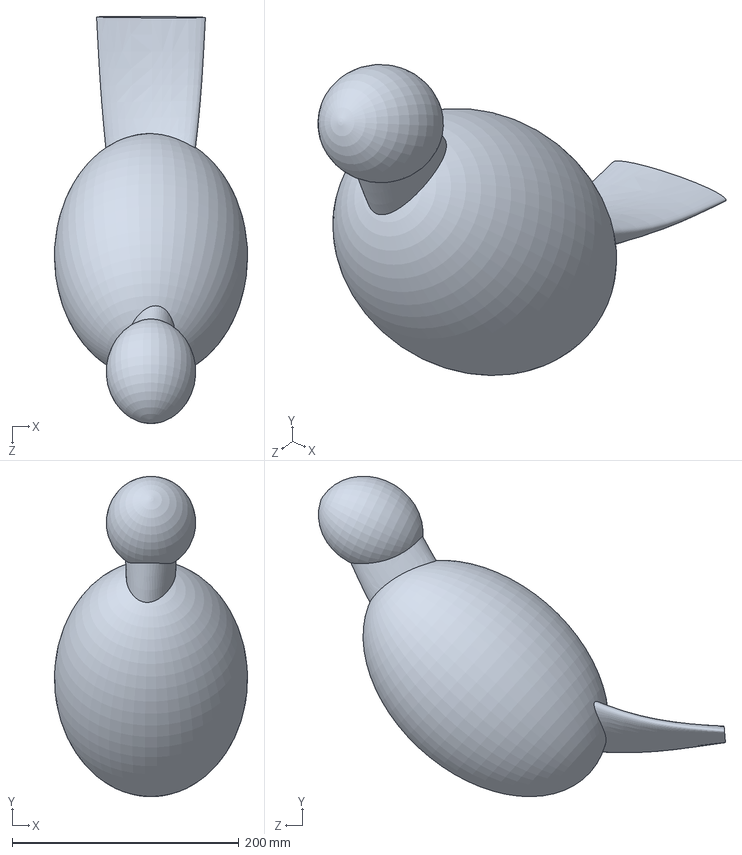
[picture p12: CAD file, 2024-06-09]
CAD files/dumpy demo bird.SLDPRT
170.3 x 282.6 x 359.2 mm

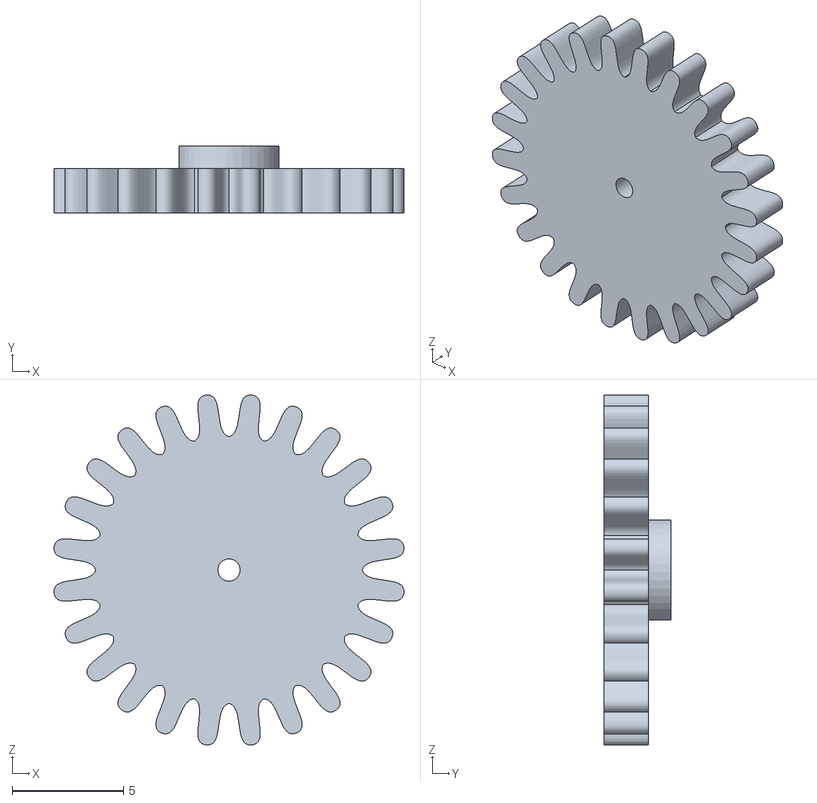
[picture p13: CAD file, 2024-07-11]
CAD files/july11_all_files/other gear.STL
15.7 x 3.00 x 15.7

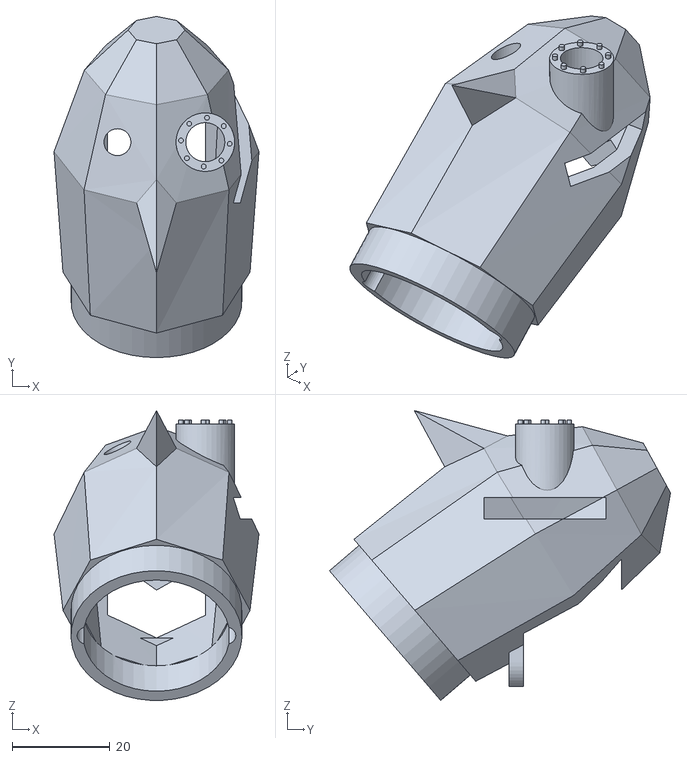
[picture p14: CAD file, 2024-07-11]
CAD files/july11_all_files/birb_head_with_flap_hole.STL
42.0 x 69.9 x 59.4

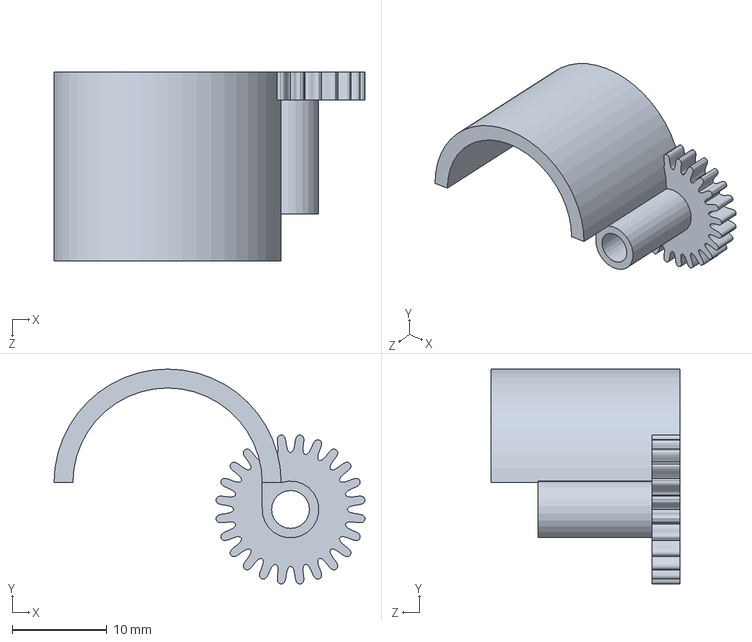
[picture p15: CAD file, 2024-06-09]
CAD files/gripper v1.SLDPRT
32.9 x 22.7 x 20.0 mm

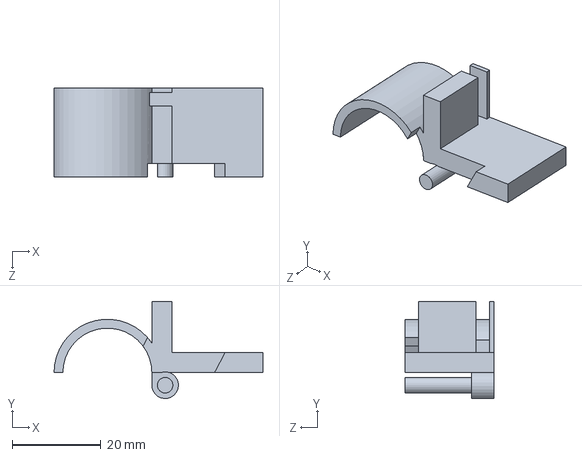
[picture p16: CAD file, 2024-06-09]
CAD files/gripper v1 part 2.SLDPRT
47.0 x 21.8 x 20.0 mm

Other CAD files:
CAD files/birb_head.STL
CAD files/other gear.SLDPRT

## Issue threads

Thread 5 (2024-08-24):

Look at pcb design

boatartist, 2024-08-24:
The prototyping board I'm using is chaotic and not very practical. I'd like to make one or two pcbs, which can go on top of the raspberry pi and maybe also another which links ports on the side so that they can be rearranged on top.

Closed 2025-07-23.

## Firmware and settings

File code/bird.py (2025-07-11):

import sys
sys.path.append('/home/pi/Desktop/galah')
import offline_tts
import display
from check_for_internet import *
import time
from wifi import *
from stt import get_speech
from picamera2 import Picamera2, Preview
from io import BytesIO
from PIL import Image, ImageDraw
import weather
from datetime import datetime
import notes
from accelerometer import ADXL345
import servo
import camera
import os

class Bird:
    wifi_modes = ['wifi', 'sim', 'none']
    non_existent_modes = ['texts']
    path = '/home/pi/Desktop/galah/'
    def __init__(self):
        os.system('sudo pigpiod')
        self.Display = display.Display()
        self.Display.switch_mode(1)
        self.Display.loading()
        self.in_menu = False
        self.mode = None
        self.speaker = True
        self.has_internet = check_for_internet()
        print('interwebs check done')
        self.wifi_mode = 'wifi'
        modem_off()
        wifi_on()
        self.prev_x, self.prev_y = 0, 0
        self.x, self.y = 0, 0
        self.has_new_input = False
        self.camera = camera.CameraApp()
        self.notes = notes.Notes()
        self.is_streaming = False
        self.is_startup = True
        self.weather_info = ['No weather data', '']
        now = datetime.now()
        print('got time')
        self.weather_time = int(now.strftime('%H%M'))
        self.now = now.strftime("%H:%M %d/%m/%Y")
        self.accelerometer = ADXL345()
        self.pitch = 0
        self.roll = 0
        self.frame = 0
        self.servo1 = servo.Servo(21)
        #some checks that the servo is working
        self.servo1.correct_angle(0)
        time.sleep(1)
        self.servo1.correct_angle(90)
        time.sleep(1)
        self.servo1.correct_angle(0)
        
    def home_page(self):
        now = datetime.now()
        current_time = int(now.strftime('%H%M'))
        self.now = now.strftime("%H:%M %d/%m/%Y")
        if current_time - self.weather_time >= 5 or self.is_startup:
            print('starting startup checks')
            try:
                weather_info = weather.get_weather()
            except:
                weather_info = ['No weather data', '']
            print('got weather, finally')
            if weather_info:
                self.weather_info = [f'{weather_info[0]}°C', weather_info[1]]
            else:
                self.weather_info = ['No weather data','']
            self.is_startup = False
            self.weather_time = current_time
        self.Display.home_screen(weather_info = self.weather_info, time = self.now, pitch = self.pitch, roll = self.roll)
        if self.has_new_input:
            self.in_menu = True
    
    def main_menu(self):
        self.Display.main_menu()
        if self.has_new_input:
            if self.x < 120 and self.y < 120:
                print('notes')
                self.Display.loading()
                offline_tts.speak('Notes', self.speaker)
                self.in_menu = False
                self.mode = 'notes'
                self.note = []
                self.note_mode = 'menu'
            elif self.x > 120 and self.y < 120:
                print('settings')
                self.Display.loading()
                offline_tts.speak('Settings', self.speaker)
                self.in_menu = False
                self.mode = 'settings'
                self.has_internet = check_for_internet()
            elif self.x < 120 and self.y > 120:
                print('camera')
                self.Display.loading()
                offline_tts.speak('Camera', self.speaker)
                self.in_menu = False
                self.mode = 'camera'
            else:
                print('sms')
                self.Display.loading()
                offline_tts.speak('Texts', self.speaker)
                self.in_menu = False
                self.mode = 'texts'
    
    def settings(self):
        self.Display.settings(self.wifi_mode, self.has_internet, self.speaker)
        if self.has_new_input:
            if self.x < 120 and self.y < 120:
                self.wifi_mode = Bird.wifi_modes[(Bird.wifi_modes.index(self.wifi_mode)+1)%3]
                if self.wifi_mode == 'wifi':
                    modem_off()
                    wifi_on()
                elif self.wifi_mode == 'sim':
                    wifi_off()
                    modem_on()
                else:
                    wifi_off()
                    modem_off()
            elif self.x > 120 and self.y < 120:
                pass
            elif self.x < 120 and self.y > 120:
                self.speaker = not self.speaker
            else:
                self.mode = None
                self.in_menu = True
    
    def camera_app(self):
        output = self.camera.update(self.Display, self.x, self.y, self.has_new_input)
        if output:
            self.Display = output
        else:
            self.mode = None
            self.in_menu = True
    
    def update(self):
        if self.frame == 50:
            self.pitch, self.roll = self.accelerometer.get_tilt_angles()
            self.servo1.correct_angle(self.roll) #ik this is backwards but the accelerometer is mounted sideways
            print(f'leaning forward {round(self.roll, 2)}°, sideways {round(self.pitch, 2)}°')
            self.frame = 0
        self.has_new_input = True
        self.x, self.y = self.Display.get_input()
        if self.x == self.prev_x and self.y == self.prev_y:
            self.has_new_input = False
        elif self.x == 0:
            self.has_new_input = False
            
        if self.in_menu:
            self.main_menu()

        elif self.mode and not self.mode in Bird.non_existent_modes:
            if self.mode == 'settings':
                self.settings()
            elif self.mode == 'camera':
                self.camera_app()
            elif self.mode == 'notes':
                self.Display, self.mode, self.in_menu = self.notes.update(self.Display, self.has_new_input, self.x, self.y, self.prev_x, self.prev_y)
        else:
            self.home_page()
        
        self.Display.update()
        self.prev_x, self.prev_y = self.x, self.y
        time.sleep(0.001)
        self.frame += 1

if __name__ == '__main__':
    bird = Bird()
    while True:
        bird.update()

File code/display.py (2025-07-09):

import time
import spidev as SPI
from PIL import Image, ImageDraw, ImageFont
from lib import LCD_1inch28, Touch_1inch28
import os
import time

class Display:
    path = '/home/pi/Desktop/galah/'
    def __init__(self, bg_colour='WHITE', font_name='Font00', font_size=24, mode=0):
        self.mode = mode
        self.bg_colour = bg_colour
        self.touch = Touch_1inch28.Touch_1inch28()
        self.disp = LCD_1inch28.LCD_1inch28()
        self.disp.Init()
        self.touch.init()
        self.touch.Set_Mode(self.mode)
        self.disp.clear()
        self.image = Image.new('RGB', (240, 240), bg_colour)
        self.draw = ImageDraw.Draw(self.image)
        self.Font = ImageFont.truetype(f'{Display.path}lib/{font_name}.ttf', font_size)
        
    def get_input(self):
        if self.mode == 1:
            self.touch.get_point()
            x = self.touch.X_point
            y = self.touch.Y_point
            return x, y
        else:
            return self.touch.Touch_Read_Byte(0x01)
        
    def switch_mode(self, mode):
        self.mode = mode
    
    def update(self):
        self.disp.ShowImage(self.image)
        
    def fill_colour(self, colour='WHITE'):
        self.draw.rectangle((0, 0, 240, 240), fill=colour, outline=None, width=1)
        
    def write(self, text='Hello World!', coordinates=(0, 0), fill='BLACK'):
        self.draw.text(coordinates, text, fill=fill, font=self.Font)
        
    def rectangle(self, coordinates=(0, 0, 240, 240), fill='RED'):
        self.draw.rectangle(coordinates, fill=fill, outline=None, width=1)
        
    def line(self, start=(0, 0), end=(0, 0), width=1, colour='BLACK'):
        self.draw.line((start, end), width=width, fill=colour)
        
    def load_image(self, file_name=None):
        if file_name:
            self.image = Image.open(file_name)
            self.draw = ImageDraw.Draw(self.image)
            
    def four_menu(self, colours=['crimson', 'cornflowerblue', 'forestgreen', 'gold']):
        self.fill_colour(colour='white')
        self.rectangle(coordinates=(0, 0, 120, 120), fill=colours[0])
        self.rectangle(coordinates=(121, 0, 240, 120), fill=colours[1])
        self.rectangle(coordinates=(0, 121, 120, 240), fill=colours[2])
        self.rectangle(coordinates=(121, 121, 240, 240), fill=colours[3])
        self.line(start=(120, 0), end=(120, 240), width=4)
        self.line(start=(0, 120), end=(240, 120), width=4)
    
    def main_menu(self):
        self.four_menu(colours=['crimson', 'cornflowerblue', 'forestgreen', 'gold'])
        self.write(text='Camera', coordinates=(4, 122))
        self.write(text='SMS', coordinates=(128, 122))
        self.write(text='Settings', coordinates=(128, 84))
        self.write(text='Notes', coordinates=(4, 84))
        
    def settings(self, wifi_mode='sim', has_internet=True, speaker=True):
        modes = ['wifi', 'sim', 'none']
        wifi_colours = ['green', 'blue', 'gray']
        wifi_colour = wifi_colours[modes.index(wifi_mode)]
        self.four_menu(colours=[wifi_colour, 'yellow', 'purple', 'red'])
        self.write(text='Wifi mode', coordinates=(4, 56))
        self.write(text=wifi_mode, coordinates=(4, 84))
        self.write(text='Interwebs?', coordinates=(128, 56))
        self.write(text='yes' if has_internet else 'no', coordinates=(128, 84))
        self.write(text='Speaker', coordinates=(4, 122))
        self.write(text='on' if speaker else 'off', coordinates=(12, 148))
        self.write(text='Exit', coordinates=(128, 122))
        
    def camera_stream(self, img):
        self.image = img
        self.draw = ImageDraw.Draw(self.image)
        
    def text_notes(self, lines=[]):
        self.fill_colour(colour='white')
        for i in range(len(lines)):
            y = i*24+48
            self.write(text=lines[i], coordinates=(30, y))
        self.rectangle(coordinates=(0, 0, 24, 240), fill='red')
        self.rectangle(coordinates=(0, 216, 240, 240), fill='green')
        self.rectangle(coordinates=(216, 0, 240, 240), fill='blue')
        self.write(text='save', coordinates=(80, 210))
        
        self.write(text='e', coordinates=(4, 64))
        self.write(text='x', coordinates=(4, 88))
        self.write(text='i', coordinates=(4, 112))
        self.write(text='t', coordinates=(4, 136))
        
        self.write(text='n', coordinates=(216, 64))
        self.write(text='e', coordinates=(216, 88))
        self.write(text='w', coordinates=(216, 112))
        
    def draw_notes(self, drawing=Image.new('RGB', (192, 192), 'white'), note=''):
        self.fill_colour(colour='white')
        self.rectangle(coordinates=(0, 0, 24, 240), fill='red')
        self.rectangle(coordinates=(0, 216, 240, 240), fill='green')
        self.rectangle(coordinates=(216, 0, 240, 240), fill='blue')
        self.write(text='save', coordinates=(80, 210))
        
        self.write(text='e', coordinates=(4, 64))
        self.write(text='x', coordinates=(4, 88))
        self.write(text='i', coordinates=(4, 112))
        self.write(text='t', coordinates=(4, 136))
        
        self.write(text='->', coordinates=(216, 64))
        
        self.write(text='X', coordinates=(216, 112))
        
        self.image.paste(drawing, (24, 24))
        self.write(text=note, coordinates=(50, 10))
        
    def notes_menu(self):
        self.four_menu(colours=['white', 'green', 'blue', 'red'])
        self.write(text='View all', coordinates=(4, 84))
        self.write(text='Dictate', coordinates=(128, 84))
        self.write(text='Draw', coordinates=(4, 122))
        self.write(text='Exit', coordinates=(128, 122))
        
    def show_notes(self, num_imgs=0):
        self.fill_colour('black')
        for i in range(num_imgs):
            img = Image.open(f'{Display.path}drawing{i}.png').resize((60, 60))
            x = i%4 * 60
            y = 60 + i//4*60
            self.image.paste(img, (x, y))
            
    def home_screen(self, weather_info='weather', icon_url='/home/pi/Desktop/galah/current_weather.png', time='00:00', pitch=0, roll=0):
        self.fill_colour('white')
        img = Image.open(icon_url).convert('RGBA').resize((60, 60))
        self.image.paste(img, (40, 40))
        self.write(text=weather_info[0], coordinates=(110, 40))
        self.write(text=weather_info[1], coordinates=(40, 100))
        self.write(text=time, coordinates=(20, 160))
        self.write(text=f'Pitch: {round(pitch, 1)}° Roll: {round(roll, 1)}°', coordinates=(20, 130))
        
    def loading(self):
        self.fill_colour('white')
        self.write(text='loading...', coordinates=(40, 100))
        self.update()
        
if __name__ == '__main__':
    d = Display()
    d.main_menu()
    d.update()
    time.sleep(5)

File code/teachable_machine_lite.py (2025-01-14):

from tflite_runtime.interpreter import Interpreter
from PIL import Image, ImageDraw, ImageFont
import numpy as np
import time
import logging

print('using this version')

class TeachableMachineLite:
    def __init__(self, model_path: str = 'model.tflite', labels_file_path: str = 'labels.txt', model_type: str = 'tflite') -> None:
        """
        Initialize the TeachableMachineLite object.

        Args:
            model_path (str): Path to the TFLite model file. Default is 'model.tflite'.
            labels_file_path (str): Path to the labels file. Default is 'labels.txt'.
            model_type (str): Type of the model. Default is 'tflite'.

        Raises:
            FileNotFoundError: If the model file is not found.
            RuntimeError: If there's an error loading the model.
        """
        self.model_path = model_path
        self.label_path = labels_file_path
        self.model_type = model_type

        self._labels = None
        self.height = None
        self.width = None
        self.interpreter = None

        self._load_labels(self.label_path)

        try:
            with open(self.model_path, 'rb') as f:
                # To check if the model file exists
                pass
        except FileNotFoundError:
            raise FileNotFoundError(f"Model file not found: {self.model_path}")

        try:
            self.interpreter = Interpreter(self.model_path)
            self.interpreter.allocate_tensors()
            logging.info(f"TeachableMachineLite Model '{self.model_path}' loaded successfully.")
            print(f"TeachableMachineLite Model '{self.model_path}' loaded successfully.")

        except Exception as e:
            error_msg = f"Error loading model '{self.model_path}': {str(e)}"
            logging.error(error_msg)
            raise RuntimeError(error_msg)
        input_details = self.interpreter.get_input_details()[0]
        _, self.height, self.width, _ = input_details['shape']


    def classify_image(self, image_path: str, calc_time: bool = False):
        """
        Classifies an image using the model interpreter and returns the classification results.

        This method loads an image from the specified file path, preprocesses it, and classifies it using the
        TFLite model interpreter. The classification result includes the predicted label, confidence score,
        and the time taken for classification if requested.

        Parameters:
        -----------
        image_path : str
            The file path to the image that needs to be classified.

        calc_time : bool, optional
            If True, measures and returns the time taken for the classification process.
            Defaults to False.

        Returns:
        --------
        dict
            A dictionary containing the classification results:
            - "id" : int
                The index of the predicted label.
            - "label" : str
                The predicted label corresponding to the image.
            - "time" : float or None
                The time taken to classify the image, in seconds (rounded to 3 decimal places).
                Returns None if `calc_time` is False.
            - "confidence" : float
                The confidence level of the classification as a percentage.
            - "highest_class_id" : int
                The same as "id", for consistency.
            - "highest_class_prob" : float
                The same as "confidence", for consistency.
        """
        image = self._load_image(image_path, return_RGB=False ,return_resized=True)

        classification_time = None

        if calc_time:
            start_time = time.time()

        label_id, prob = self._predict(image, 1)[0]

        if calc_time:
            classification_time = np.round(time.time() - start_time, 3)

        classification_label = self._labels[label_id].strip()
        classification_confidence = np.round(prob * 100, 2)

        return {
            "id": label_id,
            "label": classification_label,
            "time": classification_time,
            "confidence": classification_confidence,
            "highest_class_id": label_id,
            "highest_class_prob": classification_confidence
        }

    def show_prediction_on_image(
            self, image_path: str, classification_result=None, calc_time: bool = False, convert_to_bgr=True
    ):
        """
        Draw the prediction results on the input image and return the modified image.

        Parameters:
        image_path (str): Path to the input image file.
        classification_result (dict, optional): Pre-computed classification result. If not provided,
            the method will classify the image using the `classify_image` method.
        calc_time (bool, optional): Whether to calculate the time taken to classify the image.
            Default is False.
        convert_to_bgr (bool, optional): Whether to convert the output image from RGB to BGR format.
            This is useful when the image will be used with OpenCV. Default is True.

        Returns:
        np.ndarray or PIL.Image.Image: The image with the prediction results drawn on it. If `convert_to_bgr`
            is True, the output is a NumPy array in BGR format. Otherwise, it's a PIL.Image.Image in RGB format.
        """
        image = self._load_image(image_path, return_RGB=True, return_resized=False)

        if classification_result is None:
            classification_result = self.classify_image(image_path, calc_time)

        class_name = classification_result["label"]
        confidence = classification_result["confidence"]
        confidence_percent_text = f"{class_name}: {confidence:.2f}%"

        draw = ImageDraw.Draw(image)
        font_size = int(image.height * 0.04)  # 4% of the image height
        font = ImageFont.truetype("DejaVuSans-Bold.ttf", font_size)
        _, _, text_width, text_height = draw.textbbox((0, 0), text=confidence_percent_text, font=font)
        position = (10, image.height - text_height - 10)

        draw.rectangle(
            [
                position[0],
                position[1],
                position[0] + text_width,
                position[1] + text_height,
            ],
            fill=(0, 0, 0, 128), )

        draw.text(position, confidence_percent_text, font=font, fill=(255, 255, 255))

        if convert_to_bgr:
            image_2_numpy_arr = np.array(image)
            # Convert RGB to BGR
            image_2_numpy_arr = image_2_numpy_arr[:, :, ::-1]
            return image_2_numpy_arr
        return image

    def classify_and_show(self, image_path: str, convert_to_bgr=True):
        """
        Classify an image and show the prediction results on the image.
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

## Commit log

2024-06-09 Create CAD files folder
2024-06-09 uploaded foot and demo bird solidworks files
    [dumpy demo bird.SLDPRT, gripper v1 part 2.SLDPRT, gripper v1.SLDPRT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]
2024-06-16 Uploaded blender stl of basic low-poly bird
    [bird_basic.stl]
2024-06-21 Uploaded bird head stl, to be improved
    [birb_head.STL]
2024-06-29 uploaded improved head
    [birb_head2.STL]
2024-07-11 uploaded all STLs
    [birb_head_flap.STL, birb_head_with_flap_hole.STL, gripper v2 main part.STL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]
2024-08-11 Update bird.py with basic camera app
2024-08-11 Update display.py with camera stream function
2024-12-09 I don't know what a gerber is but i made a pcb :)
2025-01-01 uploaded new gerber
2025-01-18 upload camera app
    working: gallery, photo, exit
    not: video
    bonus: video instead crashes code as exit route
    [camera.py]
2025-07-09 Update bird.py accelerometer
2025-07-09 Update display.py to show pitch and roll
2025-07-09 Update bird.py with correct accelerometer orientation
    [bird.py]
2025-07-11 Update bird.py with working balancing servo
2025-07-11 Update servo.py with no jitter and correct angle setting
